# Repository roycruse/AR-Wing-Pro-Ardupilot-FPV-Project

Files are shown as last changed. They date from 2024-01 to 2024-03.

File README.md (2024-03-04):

# AR-Wing-Pro-Ardupilot-FPV-Project
Auto Launch now tested a few times and autotune has now been run to set PIDs.
Compass is currently disabled due to out of range errors all the time - will re-visit in the future.
Im getting what i beleive to be, early, low battery warnings so need to explore if amp draw compensated battery voltages can be used to trigger this or not as im only getting 30 minute flight times before RTL is triggered.  But oither than this - very happy with flight characteristics and performance.
## Current Hardware
- Airframe:             SonicModell AR Wing Pro (White "Falcon" PNP Edition)
  - Motor:                included SonicModell 2216-1400KV
  - ESC:                  included SonicModell 40A w/5V 3A BEC with XT60
  - ~~Servos (x2):          included 2pcs 9g metal gear servo (the gears were stripped on these "metal gear" servos.. they sare only partially metal geared)~~
  - Servos (2x):          Emax ES08MD metal geared servos
- Propeller:            Aeronaut Cam Carbon 8 x 5 folding with Mayatech 5mm hub (ebay)
- Receiver:             TBS nano pro with immortal antenna
- Transmitter:          Radiomaster TX16S mkII Max (JB Edition) with TBS Crossfire Micro TX v2 module
  - TX16S running Edge TX 2.9.2
  - Crossfire Module running firmware 6.31
- Flight Controller:    Matek H743 Slim v3
  - running firmware ardupilot 4.4.4
- GPS / Compass:        Matek M10Q-5883
- Airspeed Sensor:      Matek Digital ASPD-4525
- Buzzer:               Matek
- Battery Monitor:      Matek Hall Current Sensor 150A
- Flight Pack:          ZOHD LIONPACK 7000mAh 4S Li-ion Battery (XT60)
- FPV VTX:              Walksnail Avatar HD Pro Micro Kit (Dual Antenna) (32GB)
- FPV VRX / Goggles:    Walksnail Avatar HD Googles X
- Onboard Action Camera GoPro Hero 8 (with 3D Printed Mount)

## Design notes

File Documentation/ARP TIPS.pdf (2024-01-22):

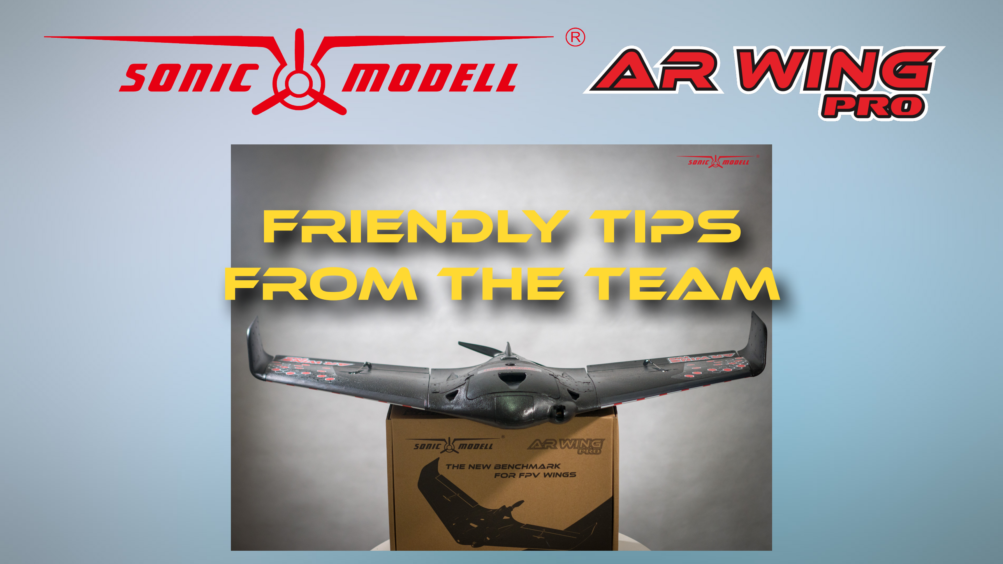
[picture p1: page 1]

# FRIENDLY TIPS FROM THE TEAM

# FRIENDLY TIPS

1. First and foremost, thanks for buying this unit. You’re not only supporting our work and families but also keeping alive a hobby that’s being threaten by all sides right now.
2. This Wing is called “PRO” for a reason. If you’re a beginner we strongly encourage you to seek advice from experience FPV pilots even before trying to put this unit together. Seriously.
3. The provided CG marks are a reference and a starting point for your tuning. It’s what worked for us after all the math and flights done. This doesn’t mean that will work for your flying style or type of mission. If you know what you’re doing, feel free to experiment with it.
4. The provided “Basic Power Combo” with the PNP version is just a “middle point” performance kit to get you in the air and have a great experience with a good balance between speed and range. If you have something specific in mind for your wing, like a super fast unit or a super long range one, we suggest you to get the KIT and use your own selected electronics. A Premium power combo will be also offered down the road.
5. In our experience the DJI FPV system was easier to setup and reply using the dedicated main hatch and placing it in the center on the wing. In any case, you can also use the side pockets and do some DIY if needed.
6. Without any doubt, this wing is BY FAR the most aerodynamic and the one with the better cooling system from all the 1 meter wings available in the market… use this advantages wisely and keep it light and clean.
7. We strongly suggest “Frisbee” style launching for this unit, as you have no grip in the bottom (precisely to keep it clean and aerodynamic)… Any other style of hand-launching could damage your fingers. Be careful.
8. This wing was meant to be flown with modern autopilot units for best performance. You can fly it manual, but you will need to have a perfect tuning for this. To improve aerodynamics and handling this design is not very forgiving to rookie mistakes or poor setup. Take your time to double check all is OK before going airborne.
9. Our best results battery wise, were with a ZOHD 4S2P 18650 7000mAh and that’s what we recommend. Having said that, if you’re a PRO, you will know what to do ;)

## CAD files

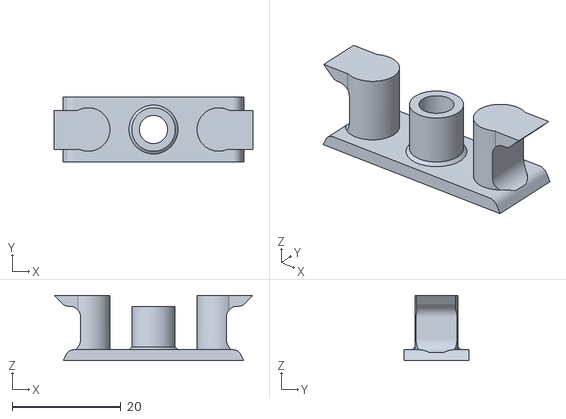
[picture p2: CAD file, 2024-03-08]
3D Printed Parts/pusher restrictor.stl
36.6 x 12.0 x 12.0

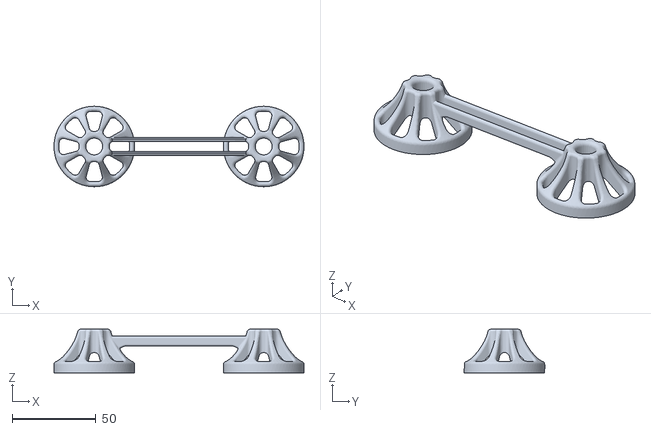
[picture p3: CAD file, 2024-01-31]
3D Printed Parts/tx16s mk2 max stick protectors.stl
149.0 x 48.0 x 26.0

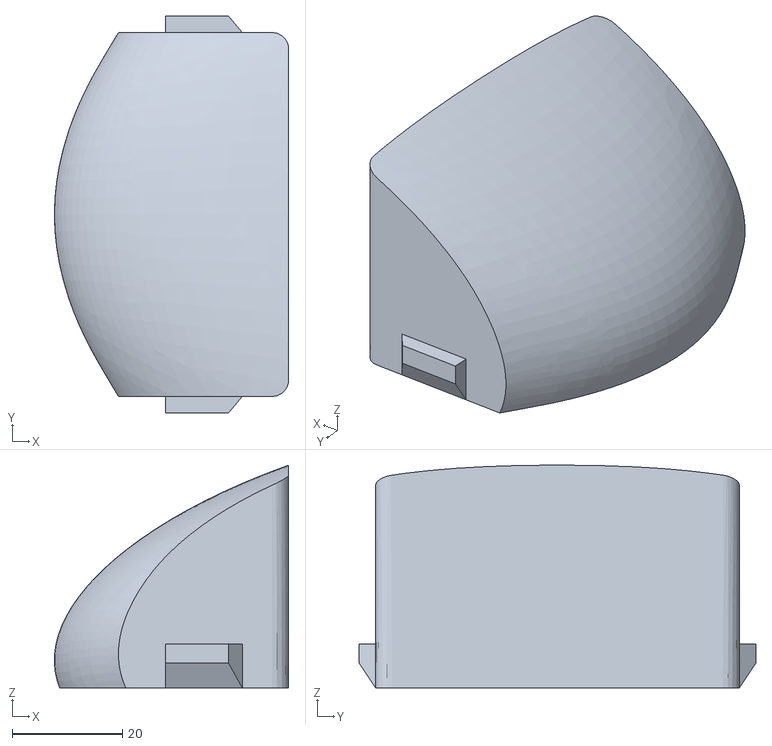
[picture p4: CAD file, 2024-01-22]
3D Printed Parts/ARP-nose.stl
42.5 x 72.0 x 40.4

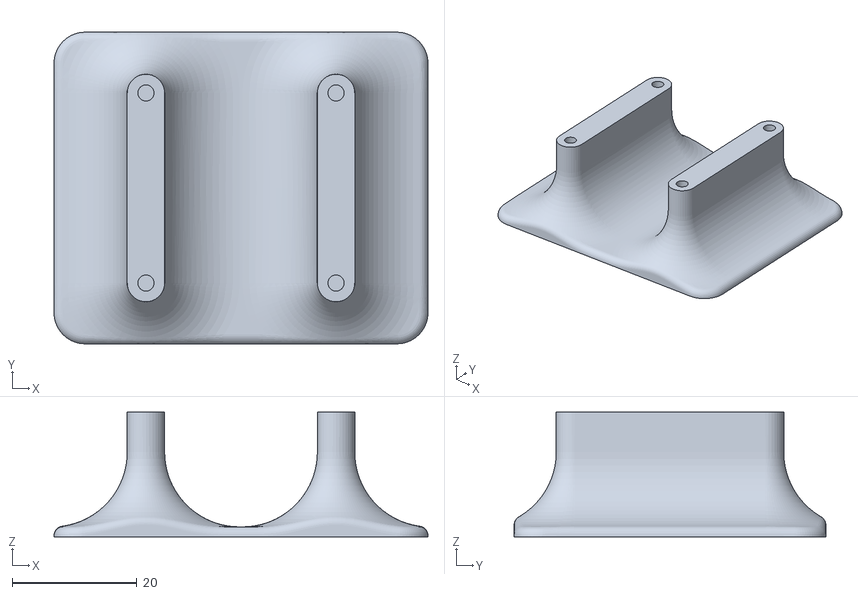
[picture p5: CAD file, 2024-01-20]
3D Printed Parts/fc mount.stl
60.0 x 50.0 x 20.0

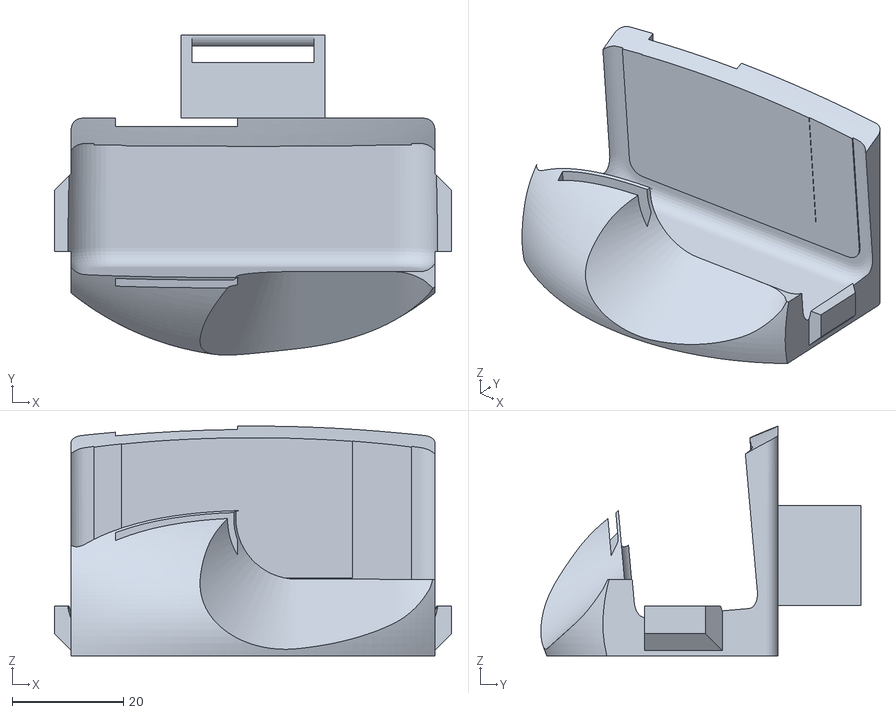
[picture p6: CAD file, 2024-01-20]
3D Printed Parts/GO PRO 8 MOUNT FOR AR WING PRO.stl
71.5 x 57.7 x 41.4

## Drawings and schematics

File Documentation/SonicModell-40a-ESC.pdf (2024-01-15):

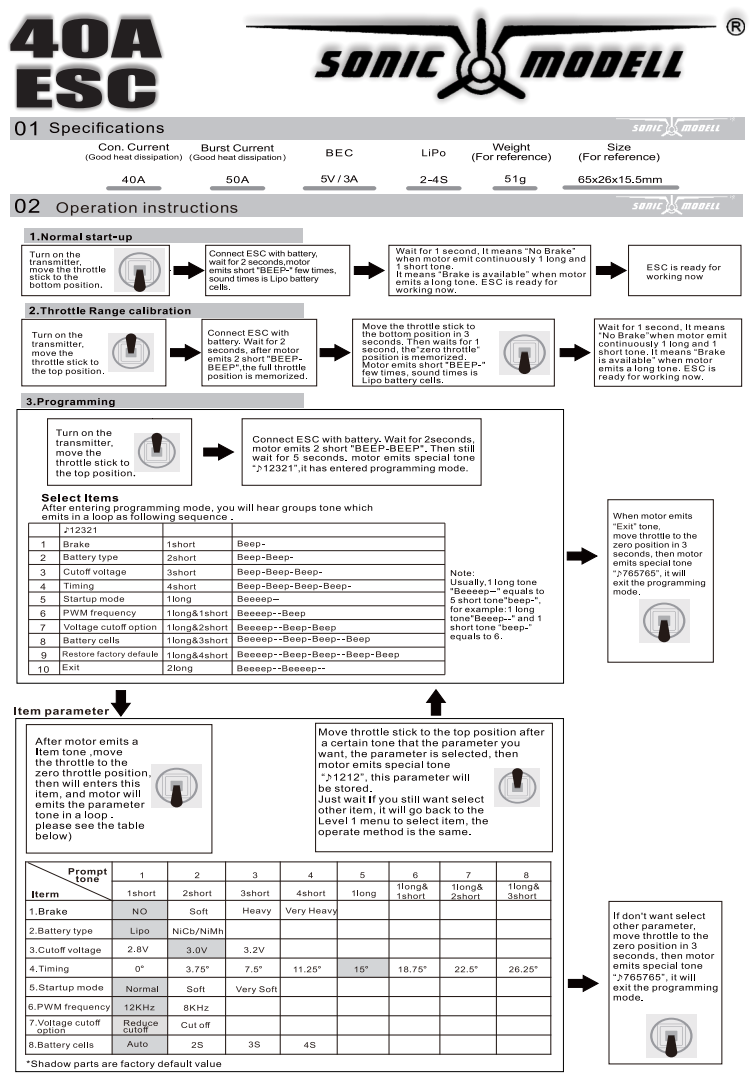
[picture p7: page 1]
40A ESC

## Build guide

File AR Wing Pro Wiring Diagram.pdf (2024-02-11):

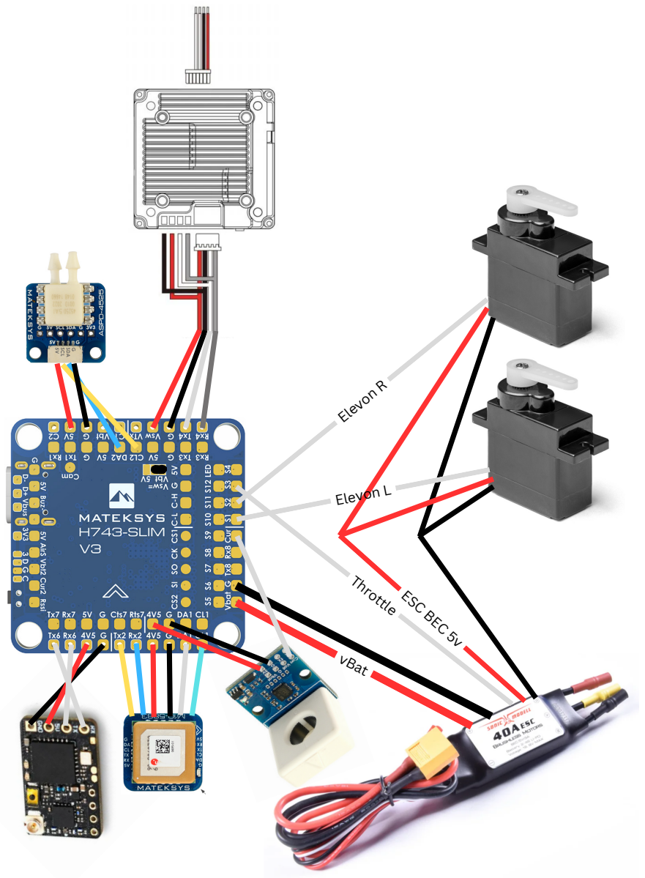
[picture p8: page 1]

vBat

ESC BEC 5v

Elevon L

Elevon R

Throttle

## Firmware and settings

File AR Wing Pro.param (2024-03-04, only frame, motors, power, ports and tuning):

BATT_AMP_OFFSET,0
BATT_AMP_PERVLT,50
BATT_ARM_MAH,0
BATT_ARM_VOLT,12
BATT_CAPACITY,7000
BATT_CRT_MAH,0
BATT_CRT_VOLT,12
BATT_CURR_PIN,11
BATT_FS_CRT_ACT,2
BATT_FS_LOW_ACT,1
BATT_FS_VOLTSRC,0
BATT_LOW_MAH,0
BATT_LOW_TIMER,20
BATT_LOW_VOLT,12.8
BATT_MONITOR,4
BATT_OPTIONS,0
BATT_SERIAL_NUM,-1
BATT_VLT_OFFSET,0
BATT_VOLT_MULT,10.5
BATT_VOLT_PIN,10
BATT_WATT_MAX,0
BATT2_MONITOR,0
BATT3_MONITOR,0
BATT4_MONITOR,0
BATT5_MONITOR,0
BATT6_MONITOR,0
BATT7_MONITOR,0
BATT8_MONITOR,0
BATT9_MONITOR,0
FLTMODE_CH,8
FLTMODE1,0
FLTMODE2,4
FLTMODE3,7
FLTMODE4,13
FLTMODE5,12
FLTMODE6,11
INS_GYRO_FILTER,20
INS_HNTCH_ENABLE,0
SERIAL0_BAUD,115
SERIAL0_PROTOCOL,2
SERIAL1_BAUD,57
SERIAL1_OPTIONS,0
SERIAL1_PROTOCOL,2
SERIAL2_BAUD,57
SERIAL2_OPTIONS,0
SERIAL2_PROTOCOL,2
SERIAL3_BAUD,38
SERIAL3_OPTIONS,0
SERIAL3_PROTOCOL,5
SERIAL4_BAUD,115
SERIAL4_OPTIONS,0
SERIAL4_PROTOCOL,-1
SERIAL5_BAUD,115
SERIAL5_OPTIONS,0
SERIAL5_PROTOCOL,-1
SERIAL6_BAUD,115
SERIAL6_OPTIONS,0
SERIAL6_PROTOCOL,42
SERIAL7_BAUD,115
SERIAL7_OPTIONS,0
SERIAL7_PROTOCOL,23
SERIAL8_BAUD,115200
SERIAL8_OPTIONS,0
SERIAL8_PROTOCOL,-1
SERVO1_FUNCTION,77
SERVO1_MAX,1900
SERVO1_MIN,1100
SERVO1_REVERSED,0
SERVO1_TRIM,1489
SERVO2_FUNCTION,78
SERVO2_MAX,1900
SERVO2_MIN,1100
SERVO2_REVERSED,1
SERVO2_TRIM,1475
SERVO3_FUNCTION,70
SERVO3_MAX,1900
SERVO3_MIN,1100
SERVO3_REVERSED,0
SERVO3_TRIM,1100
SERVO4_FUNCTION,0
SERVO4_MAX,1900
SERVO4_MIN,1100
SERVO4_REVERSED,0
SERVO4_TRIM,1500
SERVO5_FUNCTION,0
SERVO5_MAX,1900
SERVO5_MIN,1100
SERVO5_REVERSED,0
SERVO5_TRIM,1500
SERVO6_FUNCTION,0
SERVO6_MAX,1900
SERVO6_MIN,1100
SERVO6_REVERSED,0
SERVO6_TRIM,1500
SERVO7_FUNCTION,0
SERVO7_MAX,1900
SERVO7_MIN,1100
SERVO7_REVERSED,0
SERVO7_TRIM,1500
SERVO8_FUNCTION,0
SERVO8_MAX,1900
SERVO8_MIN,1100
SERVO8_REVERSED,0
SERVO8_TRIM,1500
SERVO9_FUNCTION,0
SERVO9_MAX,1900
SERVO9_MIN,1100
SERVO9_REVERSED,0
SERVO9_TRIM,1500

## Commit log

2024-01-15 Rename SonicModell-40a-ESC.pdf to Documentation/SonicModell-40a-ESC.pdf
    moving docs to documentation folder
2024-01-20 Rename GO PRO 8 MOUNT FOR AR WING PRO.stl to 3D Printed Parts/GO PRO 8 MOUNT FOR AR WING PRO.stl
    [GO PRO 8 MOUNT FOR AR WING PRO.stl]
2024-01-31 Rename tx16s mk2 max stgick protectors.stl to tx16s mk2 max stick protectors.stl
    [tx16s mk2 max stick protectors.stl]
2024-01-31 Update AR Wing Pro.param
    [AR Wing Pro.param]
2024-02-01 Add files via upload
    Odd configured
    [AR Wing Pro.param]
2024-02-04 after very sketchy maiden
    auto trim settings is the only real update - but auto launch and return to home proven to work if not optimised.
    [AR Wing Pro.param]
2024-02-12 Add files via upload
    config changes adfter crash on auto launch in still air. not enough airspeed and lost height.
    increased max throttle from 95 to 100
    increased pre rotation angle to 7.5
    decreased rotation speed to 10m/s
    increased climb out angle to 20 deg
    [AR Wing Pro.param]
2024-02-21 Add files via upload
    replaced servos so reset auto trim ready for next maiden
    [AR Wing Pro.param]
2024-03-04 Auto tuning complete
    [AR Wing Pro.param]
2024-03-04 re-instated cruise flight mode
    [AR Wing Pro.param]
